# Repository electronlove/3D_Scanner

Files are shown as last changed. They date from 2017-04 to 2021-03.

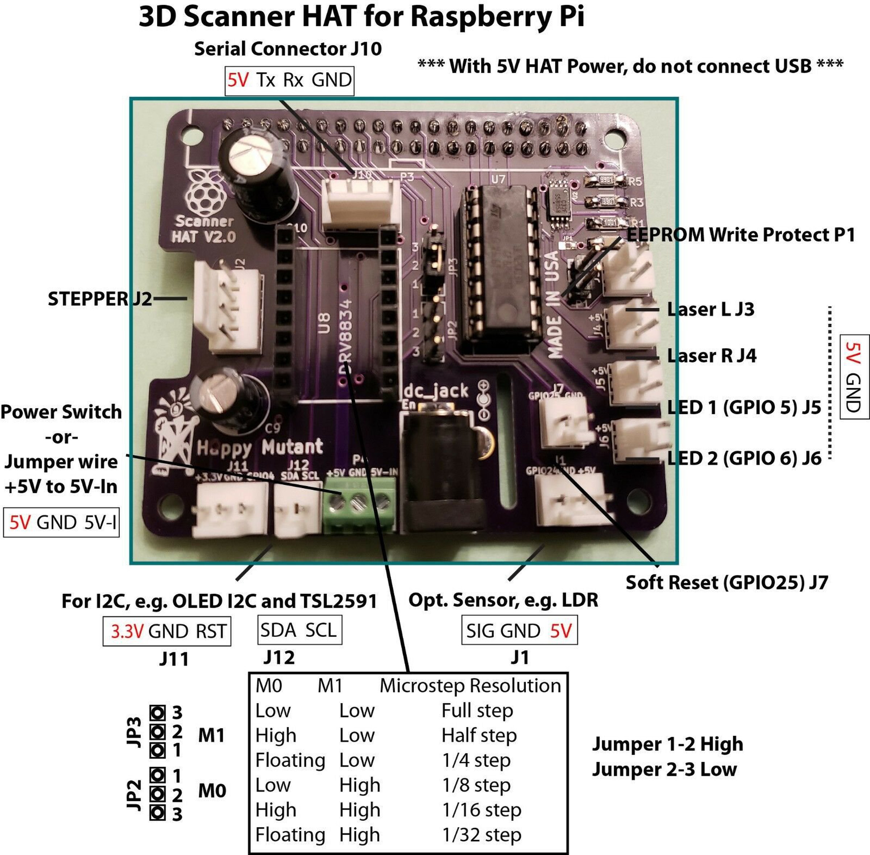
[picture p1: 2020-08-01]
Scanner Board Pinout.jpg

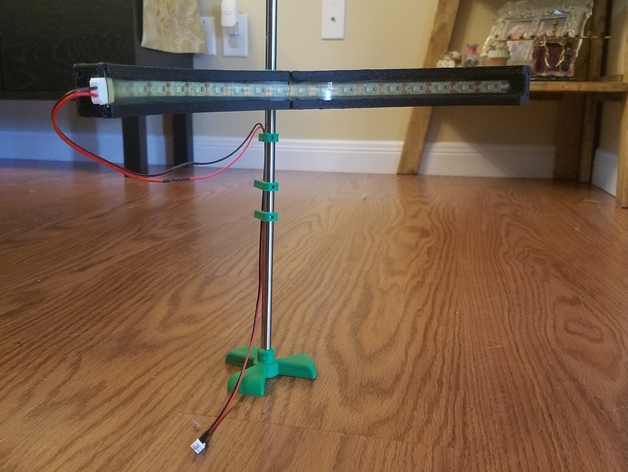
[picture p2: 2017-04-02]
LED_ARRAY/LED Array Assembly Off.jpg

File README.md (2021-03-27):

# 3D_Scanner

**Files and Settings for 3D scanner HAT**

Note that updated version of FreeLSS (Version 1.22) is available and works under Raspbian BUSTER. Updated FreeLSS version also permits use of higher pin designations (e.g. for lighting). After installing FreeLSS, ensure that PIN settings specific to 3D scanner board are correct and that steps/rotation are correct (depending on how the board is jumpered). For proper scanning, the motor should rotate counter-clockwise during scanning!  

**This 3D Scanner is based upon two open-source 3D scanning projects**: 

     FreeLSS Atlas 3D Scanner by Uriah Liggett: http://www.freelss.org/ and https://www.kickstarter.com/projects/1545315380/atlas-3d-the-3d-scanner-you-print-and-build-yourse/description 

-and- 

     Ciclop 3D Scanner by BqLabs http://diwo.bq.com/en/tag/ciclop/ and http://www.thingiverse.com/thing:740357.  

  The Atlas 3D Scanner allowed one to 3D print the majority of the components to build the scanner and ran on a Raspberry Pi and an interface board to control the lasers and turntable. The software, FreeLSS runs an HTTP server which can be accessed from any computer on your home or office network. Images acquisition is through the fixed-focus 5MP Raspberry Pi camera. In contrast, the BqLabs Ciclops 3D Scanner runs on an Arduino Uno and an interface board that requires a direct connection to a PC and utilizes a Logitech USB webcam. 
  
  The Piclop 3D Scanner (http://www.thingiverse.com/thing:754003) combines features of both projects to create a more customizable set of hardware.  The 3D Scanner HAT, conforms to the Raspberry Pi specification for HATs with a user-programmable EEPROM, cut-outs for the camera and display interface, 11 mm spacing between the HAT and the Raspberry Pi, and a 3.5 amp polyfuse for over-current protection.  An earlier version of this HAT also incorporated back-power protection, however it is no longer present in the current board version.  The board has a standard Pololu stepper driver socket (low-voltage DRV8834), jumpers to select for microstepping depending on the choice of stepper motor (0.9 or 1.8 degrees).  There are several additional connectors for: 

1. Two LED arrays
2. I2C interface for OLED displays and digital luminosity sensors (tsl2561 and tsl2591), e.g. https://www.adafruit.com/products/1980
3. Serial communication through a USB-TTL Serial interface, e.g. https://www.adafruit.com/product/954
4. Breakout for additional sensors
5. DC power connector for a 5V, 4A power supply
6. Screw terminal for power switch, e.g. https://www.adafruit.com/products/915
  
**Default settings in FreeLSS for this board**

1. Right Laser - 4
2. Left Laser  - 0
3. Steps       - 6400
4. Motor En    - 1
5. Motor Step  - 2
6. Motor Dir   - 3
7. Lighting - 21 or 22 - In Older version of the FreeLSS software, max pin number was set to 7.  FreeLESS is configured for 1 LED currently.  

*Note: This can be changed by increasing 7 to 22 in line 42 of file HttpServer.cpp (/freelss/src). You will need to make clean and recompile after changing this value.  This does not need to be done in the most recent release, version 1.22

8. All other settings stay the same. 

9. If you enable autostart "make startup", these setttings will not be present at boot.

*Note: This may not be an issue with the most recent release, version 1.22

     The TSL2591 is implemented as a systemd process that runs at boot to output digital luminosity readings to an OLED display. Preference may be to have information displayed in FreeLSS software but has not been implemented.  

Fun alternative - with a LDR input: controlling output of Darlington through either LS1/LS2 or LED1/LED2 output: https://youtu.be/d3qYswq6j8c

**Additional Notes**: Under Raspbian STRETCH through BUSTER the OLED does not initialize when RST pin is set to GPIO24 and should use GPIO4. For V1 scanner boards, this would correspond to the GPIO breakout for header # J1. In the V2 Scanner boards, GPIO4 breakout has been moved to header J11 next to SDA/SCL pinout (header J12). Voltage output at header J11 has also been changed to provide 3.3V output. Please note changes in script files for OLED display.

** You can now purchase PCBs for the 3D scanner HAT from OSH Park.  See https://oshpark.com/shared_projects/FvgkGJDE ** AND BOM file

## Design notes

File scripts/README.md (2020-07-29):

To autostart on boot:

1. Create a configuration file for OLED.service:
- sudo nano /lib/systemd/system/OLED.service

2. Enter the following information into the file:

[Unit]
- Description=OLED Status Monitor
- After=multi-user.target

[Service]
- Type=idle
- ExecStart=/usr/bin/env python /home/pi/sensor/OLED_service.py <--- Make sure the directory is correct.

[Install]
- WantedBy=multi-user.target

3. Save and exit the editor.

4. Set permissions by:
- sudo chmod 644 /lib/systemd/system/OLED.service

5. Configure the service
- sudo systemctl daemon-reload
- sudo systemctl enable OLED.service

6. Reboot
- sudo reboot

7. Check the status of the running service
- sudo systemctl status OLED_service.py

8. Imporant note:  OLED_service.py file should match the RST pin, which is 24 for older version scanner boards and 4 revised boards.

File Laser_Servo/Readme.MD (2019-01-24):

**Assembly Instructions for Servo-Mounted Line Lasers**

Servo mounting assembly for line laser.

- The servo disk mount is designed to accommodate 25T micro servo. Plate is 25mm round with 4 x 12 mm hole spacing. Screws onto servo with a button M3 screw.  

- The servo mounts were designed for MG996R servos but should fit similarly sized servos.  The servo mounts screw into the disks with 3mm button screws.

- The laser mount will accommodate 12mm laser modules. For this purpose, I used Aixiz line lasers, e.g. see http://www.aixiz.com/store/product_info.php/cPath/54/products_id/382

- The assembly is desinged to mount onto a 3D Laser Scanner to improve focus.

- Parts can be printed at 35% infill.  Supports are recommeded for the servo mounts if bridging is not optimized.

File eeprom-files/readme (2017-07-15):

To program the EEPROM 

1. Edit your /boot/config.txt file
2. Add the following paramter at the end of the file: dtparam=i2c_vc=on
3. Reboot

4. Enter into the eepromutils folder
5. Flash the eeprom with the *.eep file: sudo ./eepflash -w -f=Name_of_your_eeprom_file.eep -t=24c32
6. To confirm that the HAT is recognized change directories to /proc/device-tree/hat/
6. For vendor info: Type "more vendor"
7. For product info: Type "more product"
8. Comment out the dtparam line
9. Reboot
10. Fin !

Info from https://www.raspberrypi.org/forums/viewtopic.php?f=29&t=108134
"Howto: Raspi HAT EEPROM and device-tree"

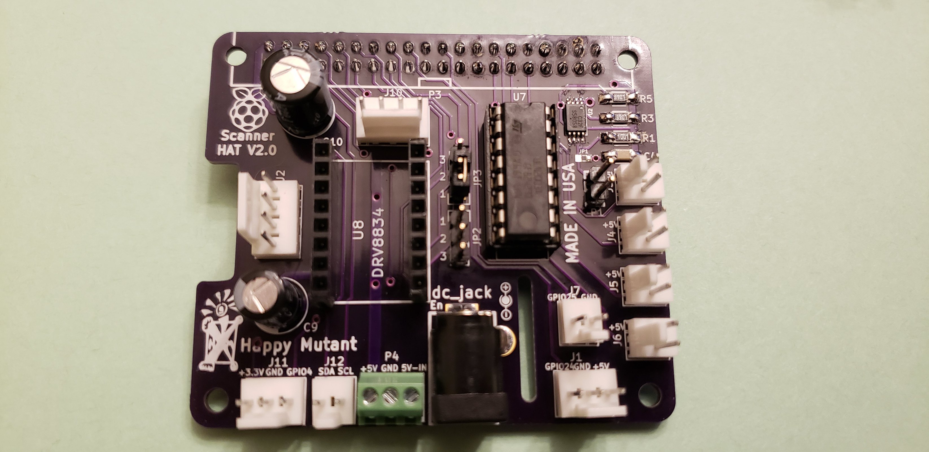
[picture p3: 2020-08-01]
Sanner Board.jpg

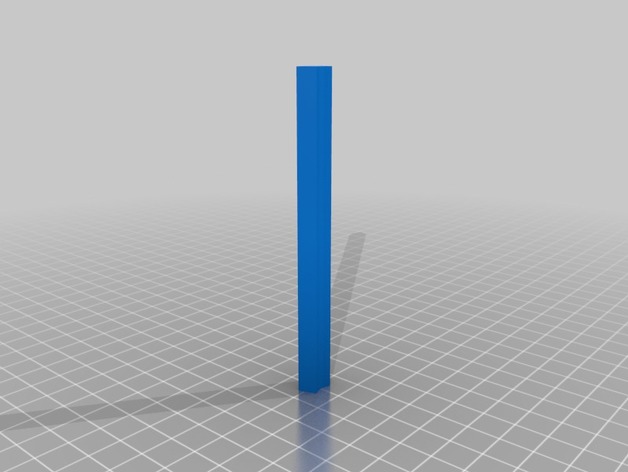
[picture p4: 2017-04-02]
TSL2591/jpegs/8a876e18ff26f397cf6693f586aebe1b_preview_featured.jpg

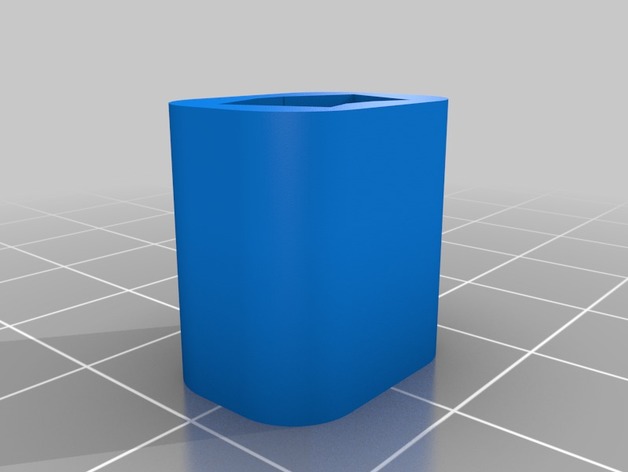
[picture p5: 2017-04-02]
TSL2591/jpegs/8a281f3cca9628e51b75e7e9b6979f1d_preview_featured.jpg

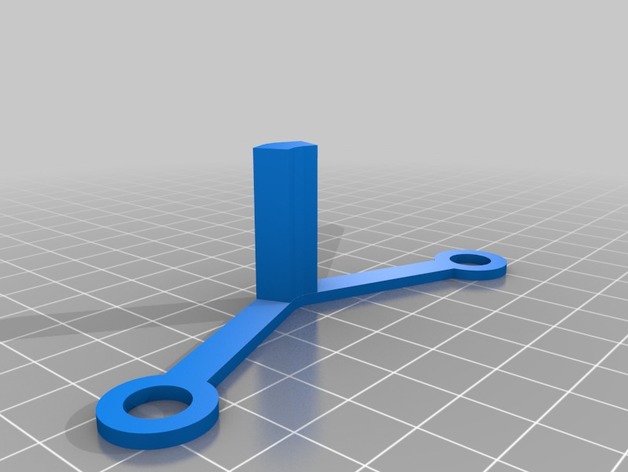
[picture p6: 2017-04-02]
TSL2591/jpegs/828e57f0cfa927053bd6b704135ffc7f_preview_featured.jpg

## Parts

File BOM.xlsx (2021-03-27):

Index | Quantity | Part Number | Manufacturer Part Number | Description
1 | 1 | WM4113-ND | 0022272041 | CONN HEADER VERT 4POS 2.54MM
2 | 1 | EJ508A-ND | EJ508A | CONN PWR JACK 2.1X5.5MM SOLDER
3 | 1 | ED10562-ND | OSTVN03A150 | TERM BLK 3P SIDE ENT 2.54MM PCB
4 | 1 | NANOSMD350LR-2CT-ND | NANOSMD350LR-2 | PTC RESET FUSE 6V 3.5A 1206
5 | 6 | WM4111-ND | 0022272021 | CONN HEADER VERT 2POS 2.54MM
6 | 2 | WM4112-ND | 0022272031 | CONN HEADER VERT 3POS 2.54MM
7 | 2 | WM4113-ND | 22272041 | CONN HEADER VERT 4POS 2.54MM
8 | 1 | CAT24C32YI-GT3OSCT-ND | CAT24C32YI-GT3 | IC EEPROM 32KBIT I2C 1MHZ 8TSSOP
9 | 1 | 1189-2262-ND | 35YXM47MEFC6.3X11 | CAP ALUM 47UF 20% 35V RADIAL
10 | 1 | S7123-ND | PPPC202LFBN-RC | CONN HDR 40POS 0.1 GOLD PCB
11 | 1 | S1011EC-40-ND | PRPC040SAAN-RC | CONN HEADER VERT 40POS 2.54MM
12 | 1 | 1189-1885-ND | 35YXF100MEFC8X11.5 | CAP ALUM 100UF 20% 35V RADIAL
13 | 1 | 609-4713-ND | DILB16P-223TLF | CONN IC DIP SOCKET 16POS TIN
14 | 1 | QPC02SXGN-RC | QPC02SXGN-RC | CONN JUMPER SHORTING .100" GOLD
15 | 1 | ULN2003A | ULN2003A | IC PWR RELAY 7NPN 1:1 16DIP
16 | 2 | P3.90KFCT-ND | ERJ-8ENF3901V | RES SMD 3.9K OHM 1% 1/4W 1206
17 | 1 | P1.00KFCT-ND | ERJ-8ENF1001V | RES SMD 1K OHM 1% 1/4W 1206
18 | 1 | 490-12564-1-ND | GRM319R71E104KA01J | CAP CER 0.1UF 25V X7R 1206

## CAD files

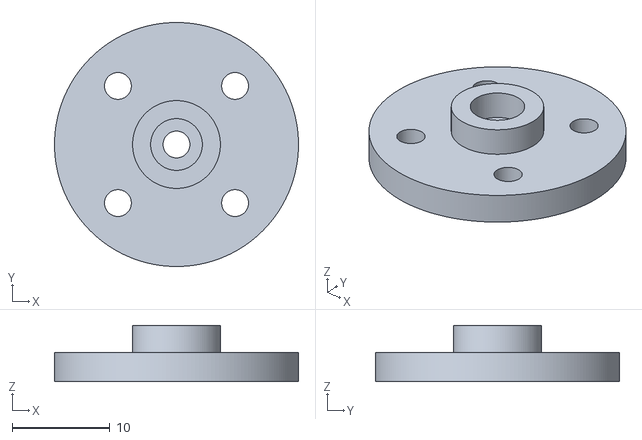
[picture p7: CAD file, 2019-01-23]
Laser_Servo/Servo Disk Mount.stl
25.0 x 25.0 x 5.75

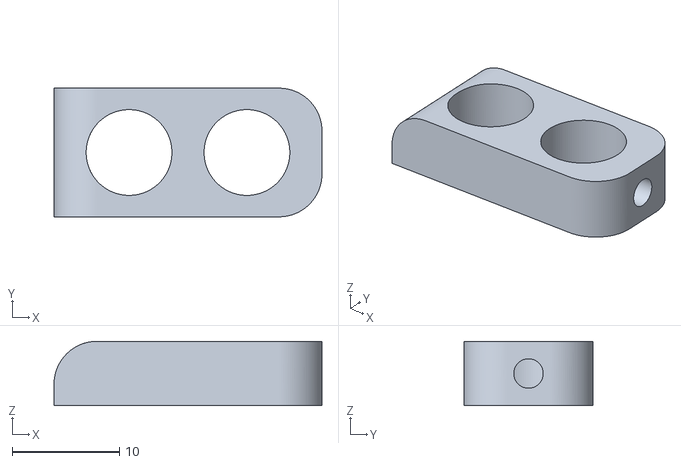
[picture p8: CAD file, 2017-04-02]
LED_ARRAY/LED_cable_management.stl
25.0 x 12.0 x 6.00

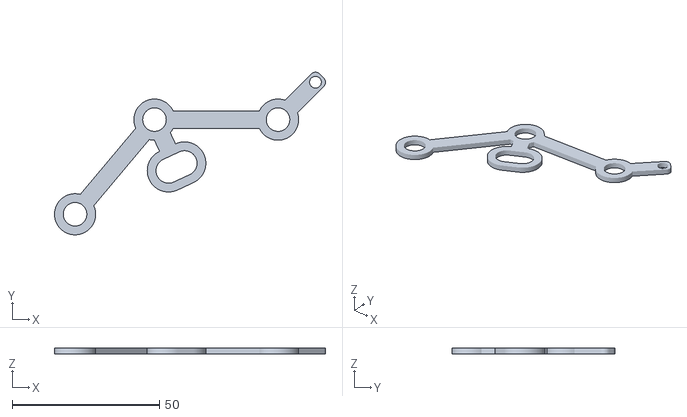
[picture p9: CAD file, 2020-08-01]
OLED/OLED arm V3.stl
92.1 x 55.3 x 2.00

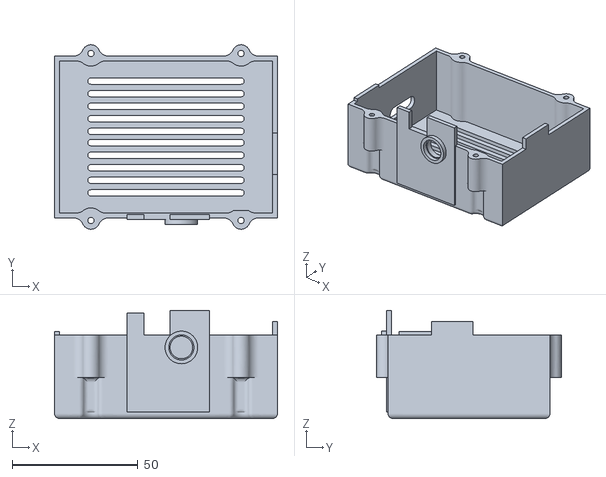
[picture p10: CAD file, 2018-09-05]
Piclop/Scanner Pi Top V2.stl
88.8 x 73.5 x 43.0

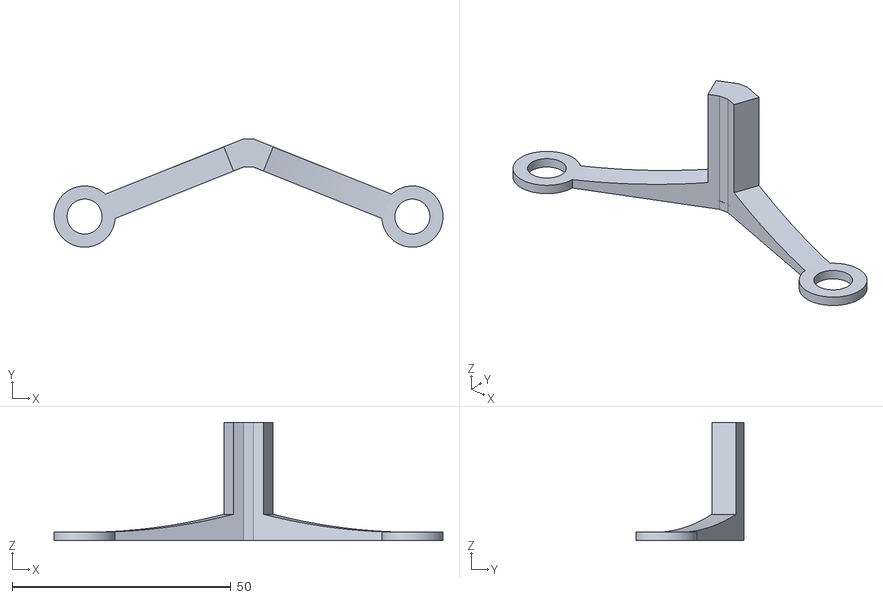
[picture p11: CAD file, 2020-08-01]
TSL2591/TSL2591 arms V2.stl
89.0 x 24.8 x 27.0

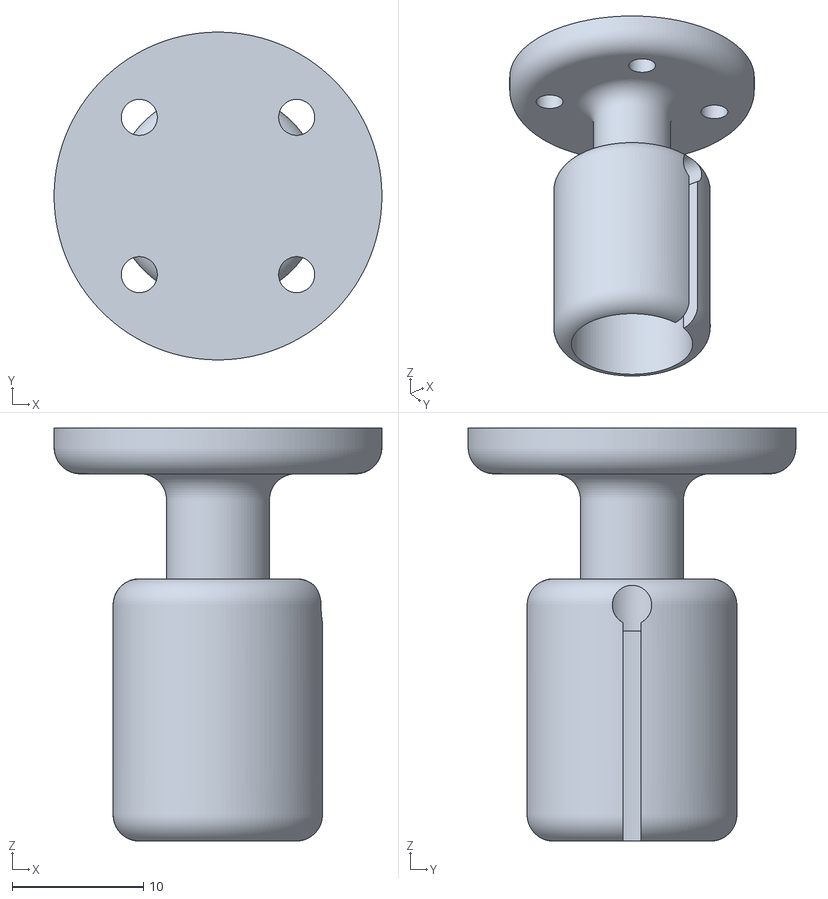
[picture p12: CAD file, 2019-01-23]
Laser_Servo/12MM laser mount.stl
25.0 x 25.0 x 31.5

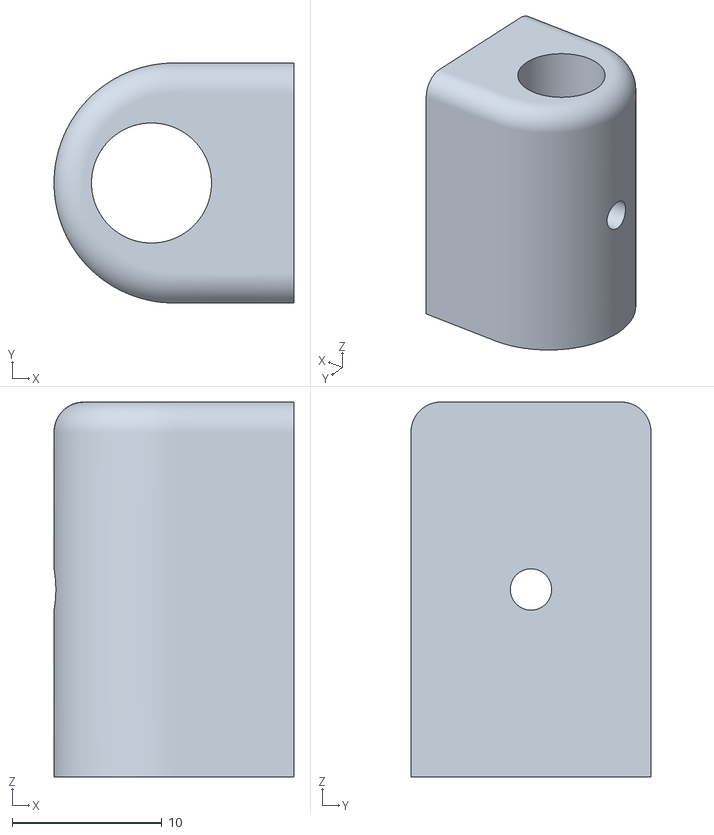
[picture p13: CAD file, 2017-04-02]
LED_ARRAY/Retention_clamp.stl
16.0 x 16.0 x 25.0

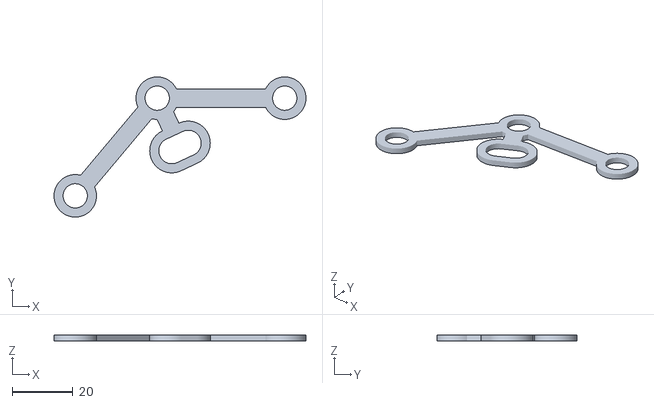
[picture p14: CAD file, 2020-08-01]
OLED/OLED arm V3 motor.stl
83.0 x 46.2 x 2.00

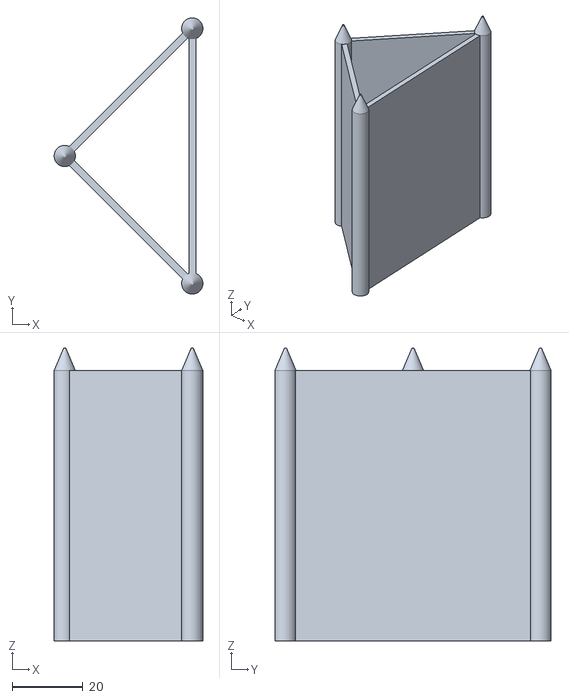
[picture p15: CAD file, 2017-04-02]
Piclop/calibration_item.stl
41.9 x 77.8 x 82.5

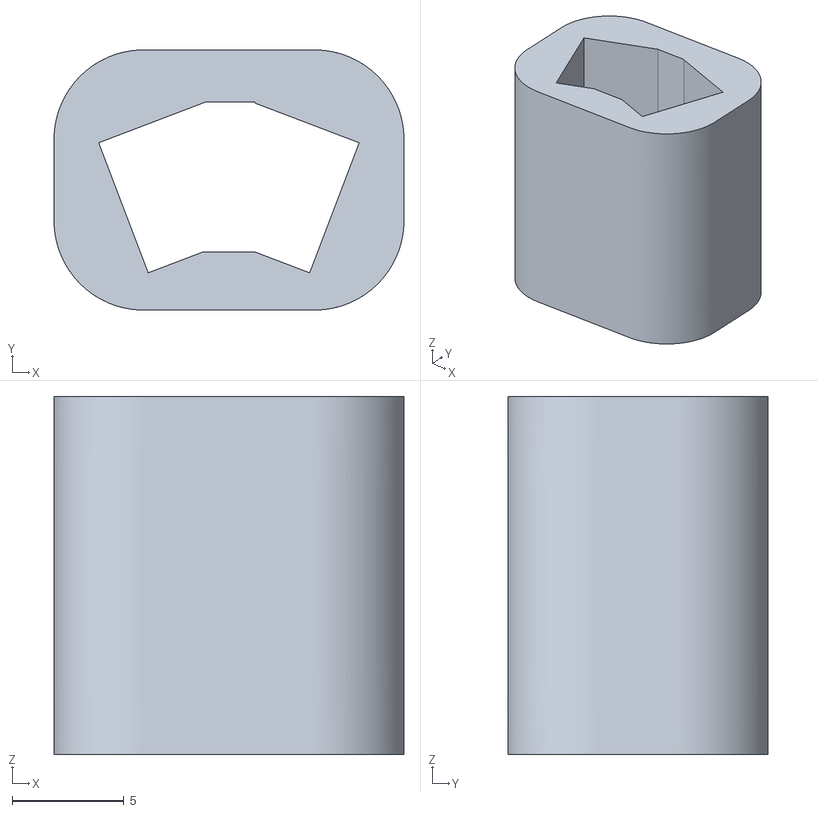
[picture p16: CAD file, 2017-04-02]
TSL2591/TSL2591_adapter.stl
15.6 x 11.6 x 16.0

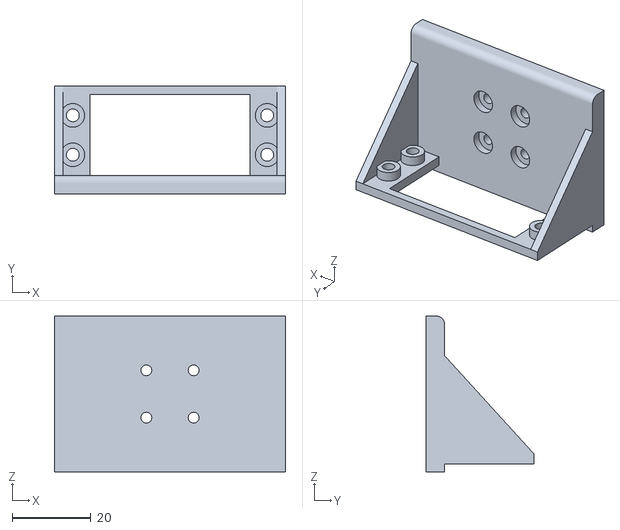
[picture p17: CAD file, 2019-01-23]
Laser_Servo/Servo Mount B.stl
58.6 x 27.5 x 39.5

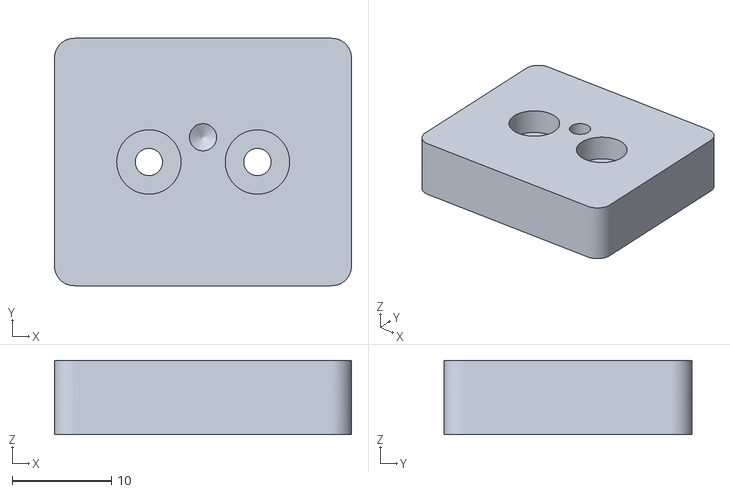
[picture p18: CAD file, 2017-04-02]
LED_ARRAY/LED_mount_plate_no_hole.stl
30.0 x 25.0 x 7.50

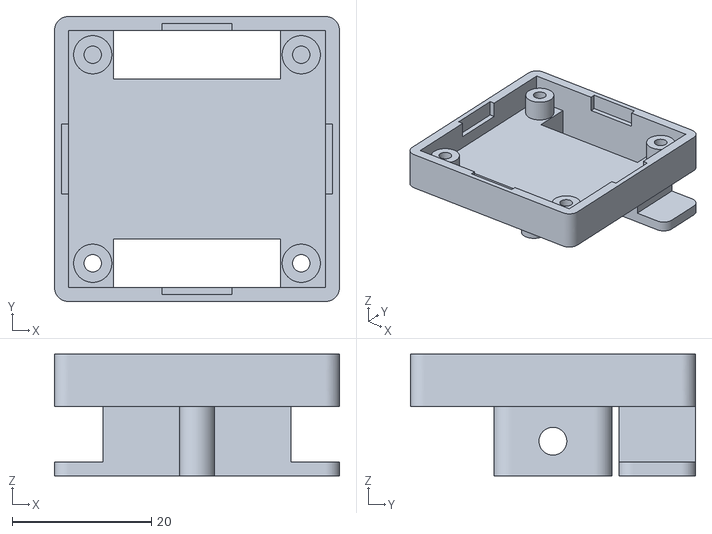
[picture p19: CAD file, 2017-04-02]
OLED/Bottom_OLED.stl
41.0 x 41.0 x 17.5

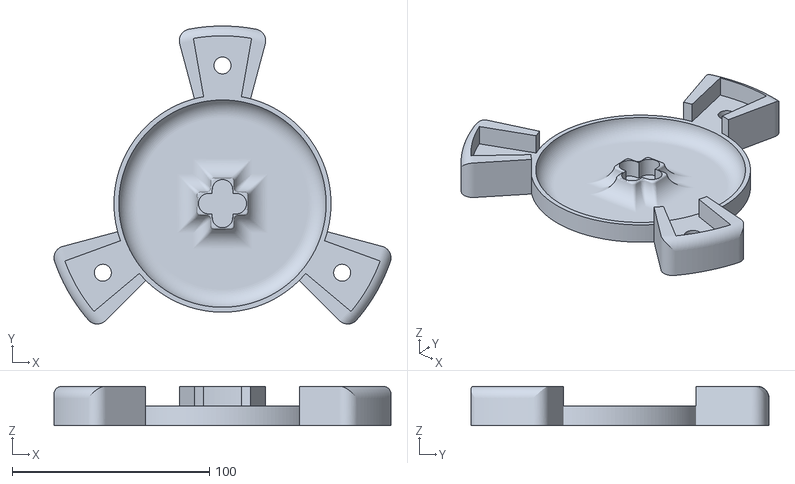
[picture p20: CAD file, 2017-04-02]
Piclop/disc-holder.stl
170.8 x 151.0 x 20.0

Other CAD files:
TSL2591/TSL2591_sensor.stl
Laser_Servo/2X Servo Mount.stl
LED_ARRAY/LED_base_8mm_mount.stl
OLED/OLED_arm.stl
LED_ARRAY/LED_Array_cuts.stl
OLED/Top_OLED_V2.stl
Piclop/Box_Raspberry.stl
Piclop/Calibration Piece 90mm.stl
Piclop/CamBox.stl
Piclop/CamBox_Back_Plate.stl
Piclop/Cover_box_Raspberry.stl
Piclop/LaserTubes.stl
Piclop/MotorTube.stl
Piclop/Pi_back.stl
Piclop/Pi_box.stl
Piclop/bearing-clip.stl
Piclop/laser_block_curved_left_1.stl
Piclop/laser_block_curved_right_1.stl
Piclop/laser_clamp_1.stl
Piclop/laser_clamp_miror.stl
Piclop/piclop_laser_holder.STL
Piclop/rpi_cable_carrier.stl
TSL2591/TSL2591_adapter_hole.stl
TSL2591/TSL2591_arms_rev.stl
TSL2591/TSL2591_mount_attachment.stl
TSL2591/TSL2591_mount_part_a.stl
TSL2591/TSL2591_mount_part_b.stl
TSL2591/TSL2591_side_arm.stl

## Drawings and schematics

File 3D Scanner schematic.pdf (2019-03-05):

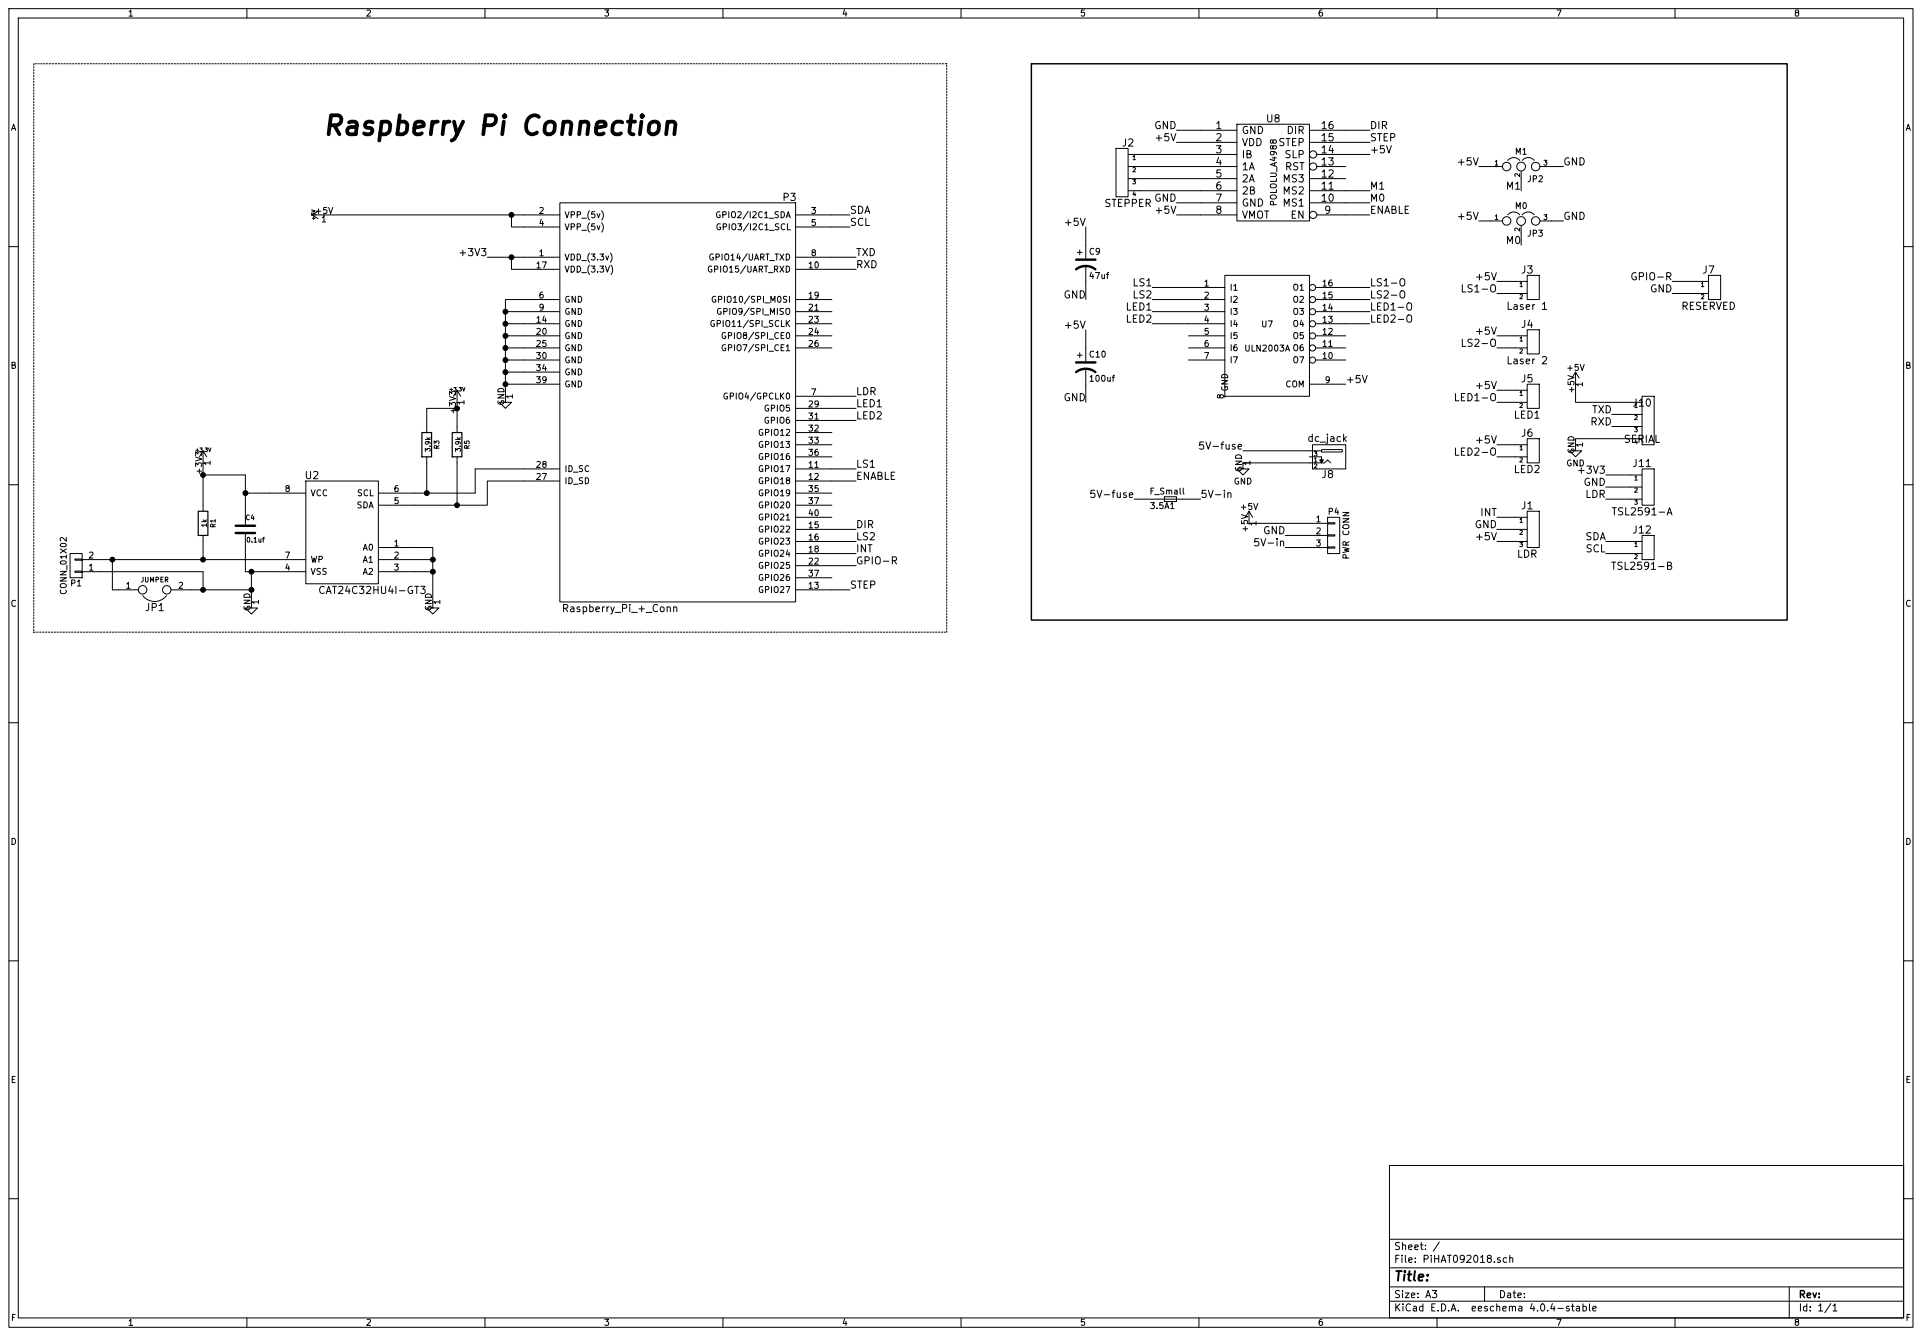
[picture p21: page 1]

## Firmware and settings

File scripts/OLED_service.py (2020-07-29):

#!/usr/bin/env python

# imports all of the required modules

import time

import sys
import socket
import fcntl
import struct
# from time import sleep

import tsl2591
import cPickle as pickle
import Adafruit_GPIO.SPI as SPI
import Adafruit_SSD1306

from PIL import Image
from PIL import ImageDraw
from PIL import ImageFont


# Raspberry Pi pin configuration:
# RST pin was previously 24 for older version scanner board

RST = 4

# Note you can change the I2C address by passing an i2c_address parameter like:
disp = Adafruit_SSD1306.SSD1306_128_64(rst=RST, i2c_address=0x3D)

# This function grabs the IP address of eth0 and wlan0
def get_ip_address(ifname):
	s = socket.socket(socket.AF_INET, socket.SOCK_DGRAM)
	return socket.inet_ntoa(fcntl.ioctl(
		s.fileno(),
		0x8915,	# SIOCGIFADDR
		struct.pack('256s', ifname[:15])
	    )[20:24])

for i in range (0,17280):
	TextLuxHeader = "Lux:"
	TextFullHeader = "Full:"
	TextIRHeader = "IR:"

	try:
		tsl = tsl2591.Tsl2591()
		full, ir = tsl.get_full_luminosity()
		lux = tsl.calculate_lux(full, ir)
		with open('/home/pi/sensor/sensor.pickle', 'w') as f:
			pickle.dump([lux, full, ir], f)
		lux = "{} LX".format(lux)
		full = "{} FULL".format(full)
		ir = "{} IR".format(ir)
	except:
		lux = ('N/A')
		full = ('N/A')
		ir = ('N/A')

	try:
		TEXTwlan = get_ip_address('wlan0')
	except IOError:
		TEXTwlan = ('NO NETWORK')

	try:
		TEXTlan = get_ip_address('eth0')
	except IOError:
		TEXTlan = ('NO NETWORK')


# Initialize library.
	disp.begin()

# Clear display.
# disp.clear()
# disp.display()

# Create blank image for drawing
	width = disp.width
	height = disp.height
	image = Image.new('1', (width, height))

# Get drawing object to draw on image.
	draw = ImageDraw.Draw(image)

# Load Font
	font1 = ImageFont.truetype('FreeSans.ttf', 13)
	font2 = ImageFont.truetype('FreeSans.ttf', 14)

	draw.text((1, 1),TextLuxHeader, font=font2, fill=255)
	draw.text((45, 1), lux, font=font2, fill=255) 
	draw.text((1, 14), TextFullHeader, font=font2, fill=255)
	draw.text((45, 14), full, font=font2, fill=255)
	draw.text((1, 27),TextIRHeader, font=font2, fill=255)
	draw.text((45, 27), ir, font=font2, fill=255)

	ipWLAN = 'WLAN:'
	ipLAN = 'LAN:'
	draw.text((45, 41),TEXTwlan, font=font1, fill=255)
	draw.text((45, 52),TEXTlan, font=font1, fill=255)
	draw.text((1, 41),ipWLAN, font=font1, fill=255)
	draw.text((1, 52),ipLAN, font=font1, fill=255)


# Display image.
	disp.image(image)
	disp.display()

	time.sleep(5)

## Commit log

2017-04-02 3D Scanner HAT front and back
    Assembled 3D scanner board. See diagram for wiring
2017-04-02 3D Scanner Board Layout
    Information for setting up the board with a Raspberry Pi.
2017-04-02 STL Files for OLED Display
    [Bottom_OLED.stl, OLED_arm.stl, OLED_front_arm.stl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]
2017-04-02 OLED Display STL Files
    [Bottom_OLED.stl, OLED_arm.stl, OLED_front_arm.stl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]
2017-04-02 OLED Sample
2017-04-02 TSL2591 Sensor STL Files
    [TSL2591_adapter.stl, TSL2591_adapter_hole.stl, TSL2591_arms_rev.stl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]
2017-04-02 TSL2591 Sensor Assembly
2017-04-02 STL Renders
2017-04-02 Piclop STL Files
    Files from 3D Scanner variants http://www.thingiverse.com/thing:754003 AND http://www.thingiverse.com/thing:1466385
2017-04-02 STL Files and info for LED Array
2017-04-02 STL Files for LED Array
    [LED_Array_cuts.stl, LED_base_8mm_mount.stl, LED_cable_management.stl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]
2017-04-02 LED Array Assembly
2017-04-02 STL files for the Piclop 3D Scanner
    The Pi_back and Pi_box will not accommodate the 3D Scanner HAT and wiring. The tower is milled to install a front illuminated power switch.
    [Calibration Piece 90mm.stl, CamBox.stl, CamBox_Back_Plate.stl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]
2017-04-02 STL files to accommodate 3D Scanner HAT and wiring
    [Box_Raspberry.stl, Cover_box_Raspberry.stl]
2017-04-02 STL Files for the turntable top
    [bearing-clip.stl, disc-holder.stl]
2017-04-02 STL File for Scanner Calibration
    This item is required for proper calibration of the 3D Scanner.
    [calibration_item.stl]
2017-04-04 Sample python script to measure luminosity
2017-04-04 Add files via upload
    3D Scanner HAT Connectors
2019-01-23 Add files via upload
    Servo mount #1 to scanner base
    [2X Servo Mount.stl]
2019-01-23 Add files via upload
    Servo Mount for Laser
    [Servo Mount B.stl]
2019-01-23 Add files via upload
    12MM laser module mount
    [12MM laser mount.stl]
2019-01-23 Add files via upload
    Servo mount - 25mm diameter + 2.5 center
    [Servo Disk Mount.stl]
2019-01-24 Add files via upload
    Line laser mounted to rotational and directional servos
2019-03-05 Add files via upload
    Schematic for V2.0 3D Scanner HAT for Raspberry Pi
    Changes include swap of BCM GPIO 4 and GPIO 24 and 3.3V breakout
2020-08-01 Add files via upload
    3D Scanner Board Version 2 - Pinouts
2020-08-01 Add files via upload
    3D Scanner Board V2 front
2020-08-01 Add files via upload
    OLED mount with routing for motor cabling
    [OLED arm V3 motor.stl]
2020-08-01 Add files via upload
    OLED mounting V3 with routing for motor.
    [OLED arm V3.stl]
2020-08-01 Add files via upload
    New version with improved stability
    [TSL2591 arms V2.stl]
